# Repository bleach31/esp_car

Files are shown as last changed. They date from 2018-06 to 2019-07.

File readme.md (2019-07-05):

View this project on [CADLAB.io](https://cadlab.io/project/1962). 

### diff drive car by esp-wroom-32

Cuddling Alexa
### software
esp32、androidはソースコードの中

microbit:https://makecode.microbit.org/_AAq7xpe3sfrz

### hardware
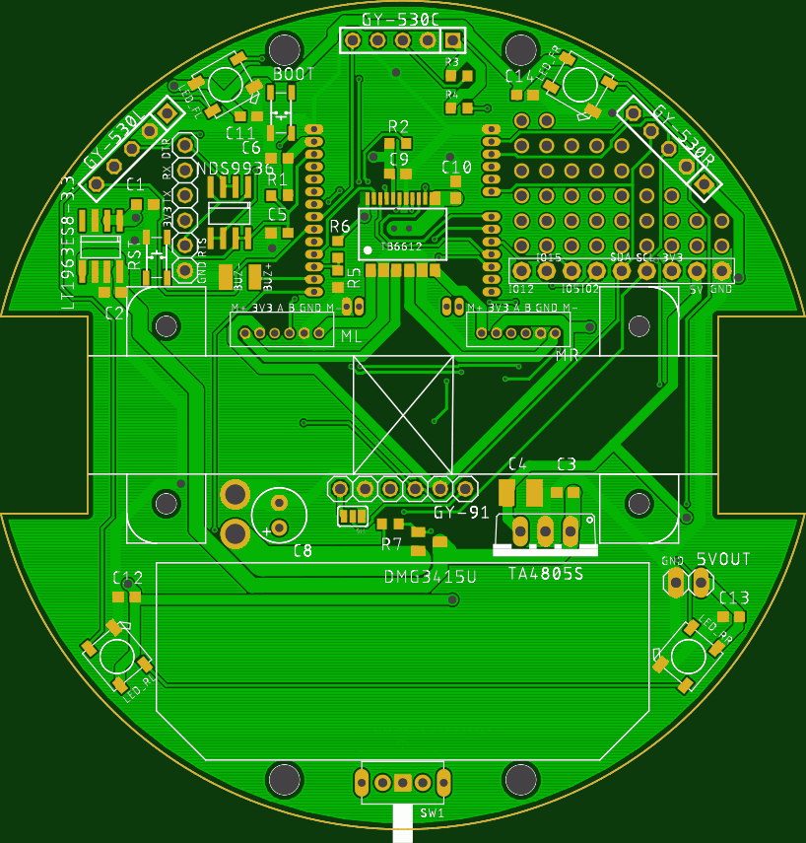
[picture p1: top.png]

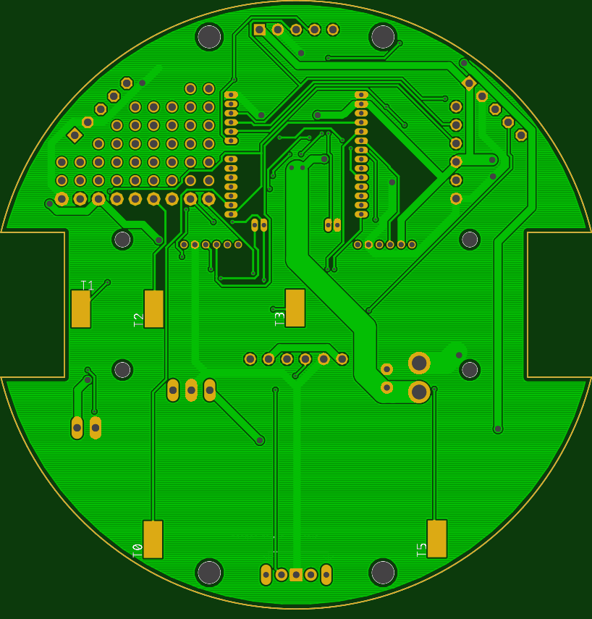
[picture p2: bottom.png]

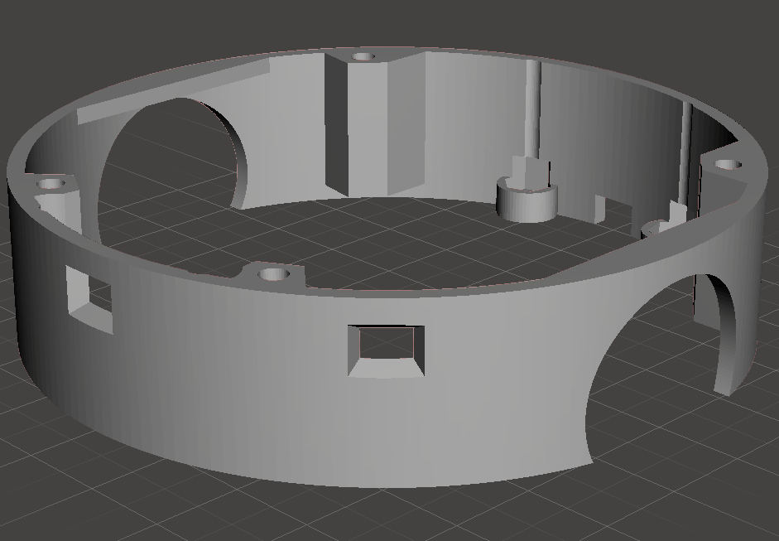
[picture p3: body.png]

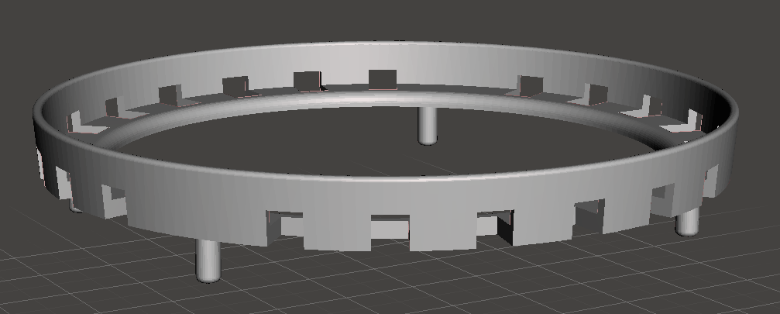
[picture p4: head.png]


モータマウント：https://www.thingiverse.com/thing:1364768
↑の12mmのやつ。

#### parts memo
- 100kオーム 1608 http://akizukidenshi.com/catalog/g/gR-11792/
- 5v 1a 縦型　 http://akizukidenshi.com/catalog/g/gI-00537/
    http://akizukidenshi.com/catalog/g/gM-13536/
    発熱がひどかったのでこっちに変更。6.5vから使えて最大1A、効率90-94%

    3.3V系統もBLEを使うと結構やばい。
    http://akizukidenshi.com/catalog/g/gM-13535/で設計すればよかった。
    
    回路設計時は入手性がよくてリポ2セル(最低6.4v)で動くスイッチングレギュレータ見つけられなかった・・・。

- 電源用mosfet http://akizukidenshi.com/catalog/g/gI-03942/
- 47uF http://akizukidenshi.com/catalog/g/gP-04657/
- 100uF http://akizukidenshi.com/catalog/g/gP-08290/
- モータードライバ　http://akizukidenshi.com/catalog/g/gI-11317/
- 3.3V 1.5A http://akizukidenshi.com/catalog/g/gI-02558/
- mos http://akizukidenshi.com/catalog/g/gI-01233/
- タクトスイッチ：http://akizukidenshi.com/catalog/g/gP-06185/
- モータコネクタzh 6pin　ｘ2：https://www.sengoku.co.jp/mod/sgk_cart/detail.php?code=4A44-P4HR
- リポ　2セル　3.7*2=7.4(6.4v-8.4v)　46ｘ20x 18未満
- LEDフルカラー4つ http://akizukidenshi.com/catalog/g/gI-07915/
- 電源コネクタ 　jstコネクタのメス
- ５Vアウトコネクタ　jstコネクタのメス　https://www.amazon.co.jp/SODIAL-R-10ペアの150mm-JSTコネクタープラグケーブルライン-オス＋メス-RC-BECリポ電池の為/dp/B00O2MPSU4/ref=sr_1_9?ie=UTF8&qid=1531495570&sr=8-9&keywords=jst
- 電源スイッチ, 横向き　http://akizukidenshi.com/catalog/g/gP-08789/
- ブザー http://akizukidenshi.com/catalog/g/gP-04497/
- アレクサ給電用microUSB:　http://www.epanorama.net/newepa/2016/04/27/qi-receiver-teardown/
- モータマウント m2 5mmぐらい4個　, M3　ネジ＋ナット　5㎜ぐらい ４個
- 距離センサ GY-530 3つ　4pin。10.5x13.3 https://www.smart-prototyping.com/VL53L0X-Time-of-Flight-Distance-Sensor-GY-530
- 9軸+気温+気圧　GY-91 (MPU9250+BMP280) 6pin　14.3mm * 20.5mm　https://electronics.semaf.at/9DOF-Axis-IMU-MPU9250-and-BMP280-Atmospheric-Sensor

1608の抵抗10k,20kとか
1608のコンデンサ0.1uF 10uFとか。

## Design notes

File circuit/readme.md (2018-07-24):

修正点メモ

バッテリー電圧検知をADC1にさす。ADC2はWifiBLEと同時使用できない。

ネジ穴をもう少し内側へ

モータコネクタとマイコンの干渉

リセットボタン押しにくい

UARTコネクタとケースの干渉

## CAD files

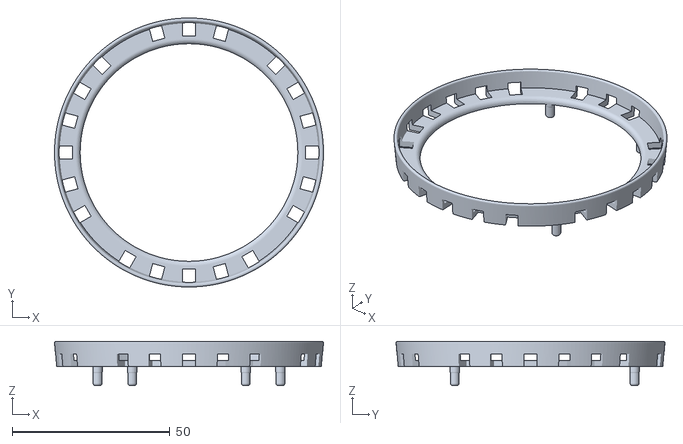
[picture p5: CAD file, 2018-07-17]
hardware/head.stl
85.3 x 85.3 x 14.0

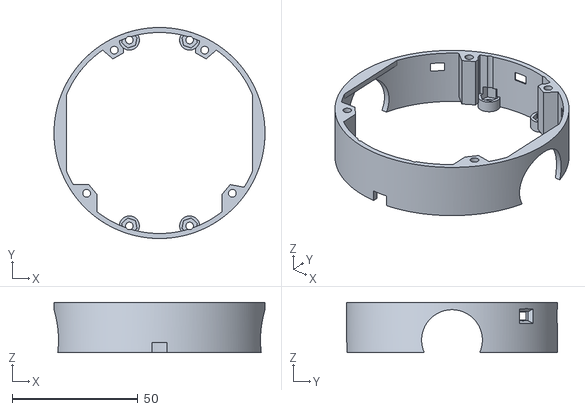
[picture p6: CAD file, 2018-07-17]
hardware/Body.stl
84.0 x 84.0 x 20.0

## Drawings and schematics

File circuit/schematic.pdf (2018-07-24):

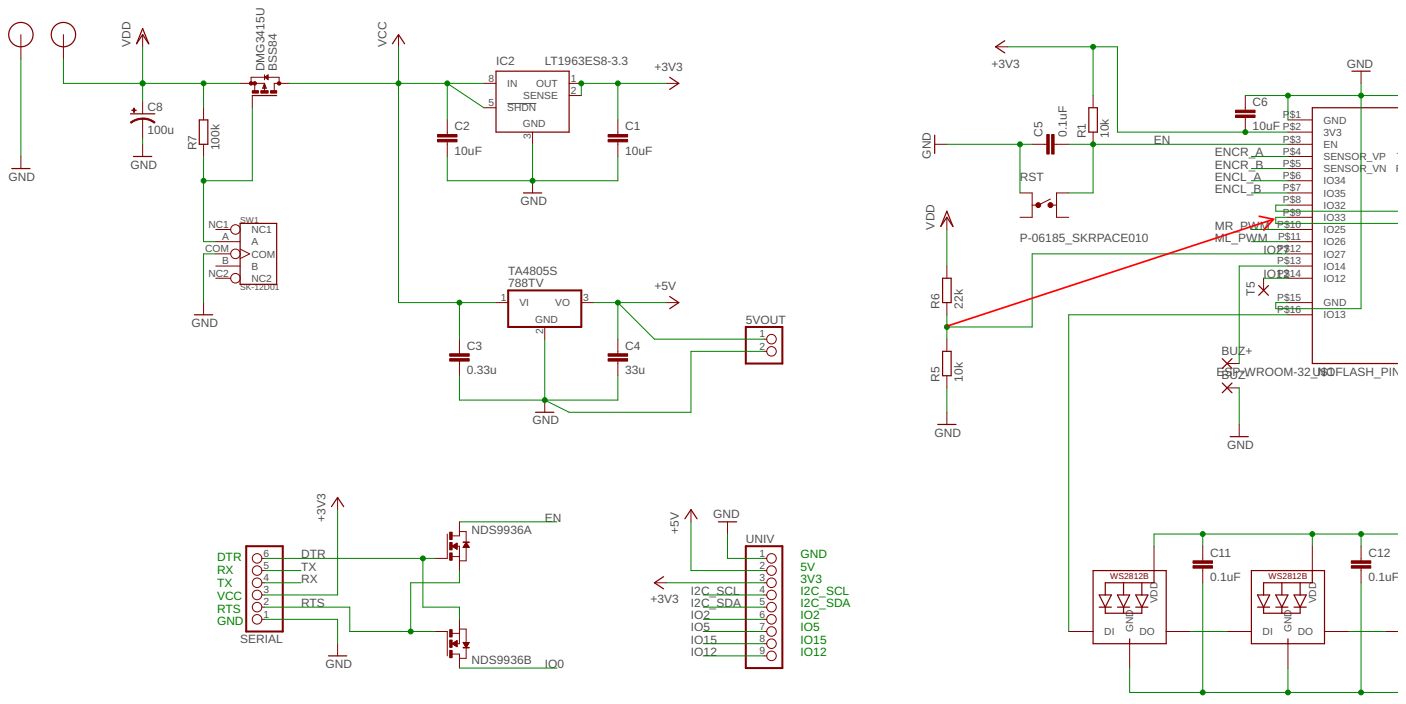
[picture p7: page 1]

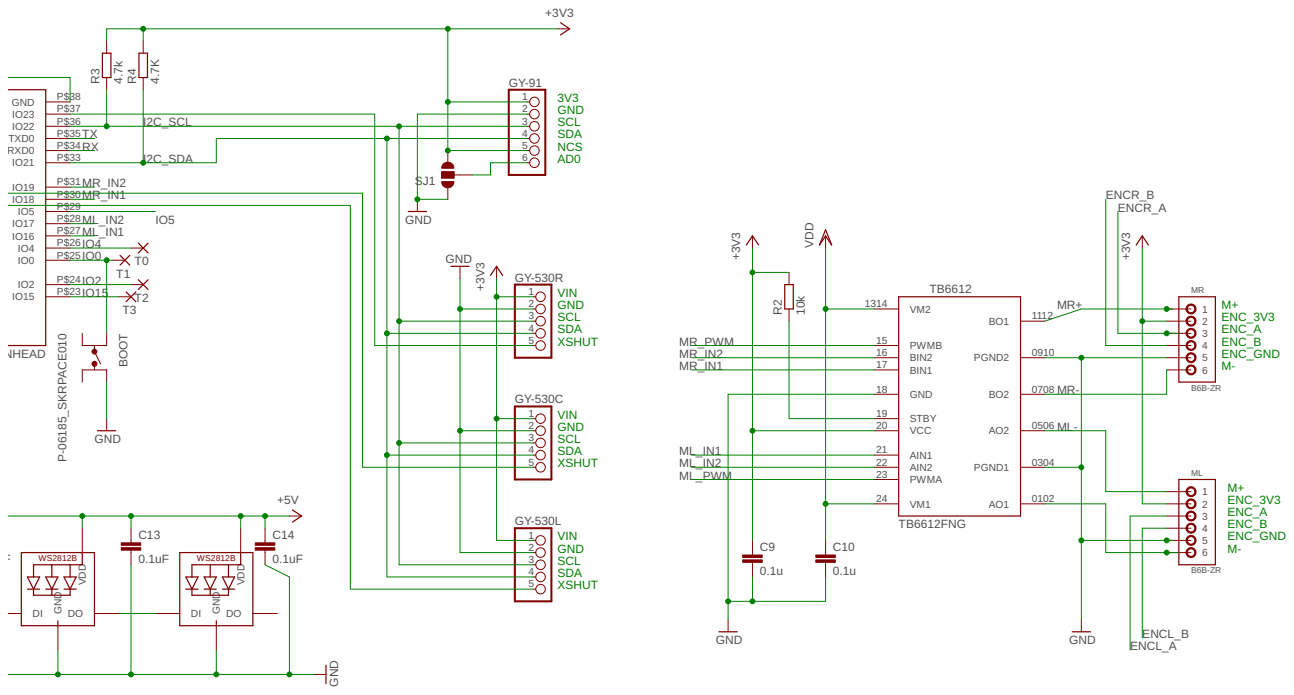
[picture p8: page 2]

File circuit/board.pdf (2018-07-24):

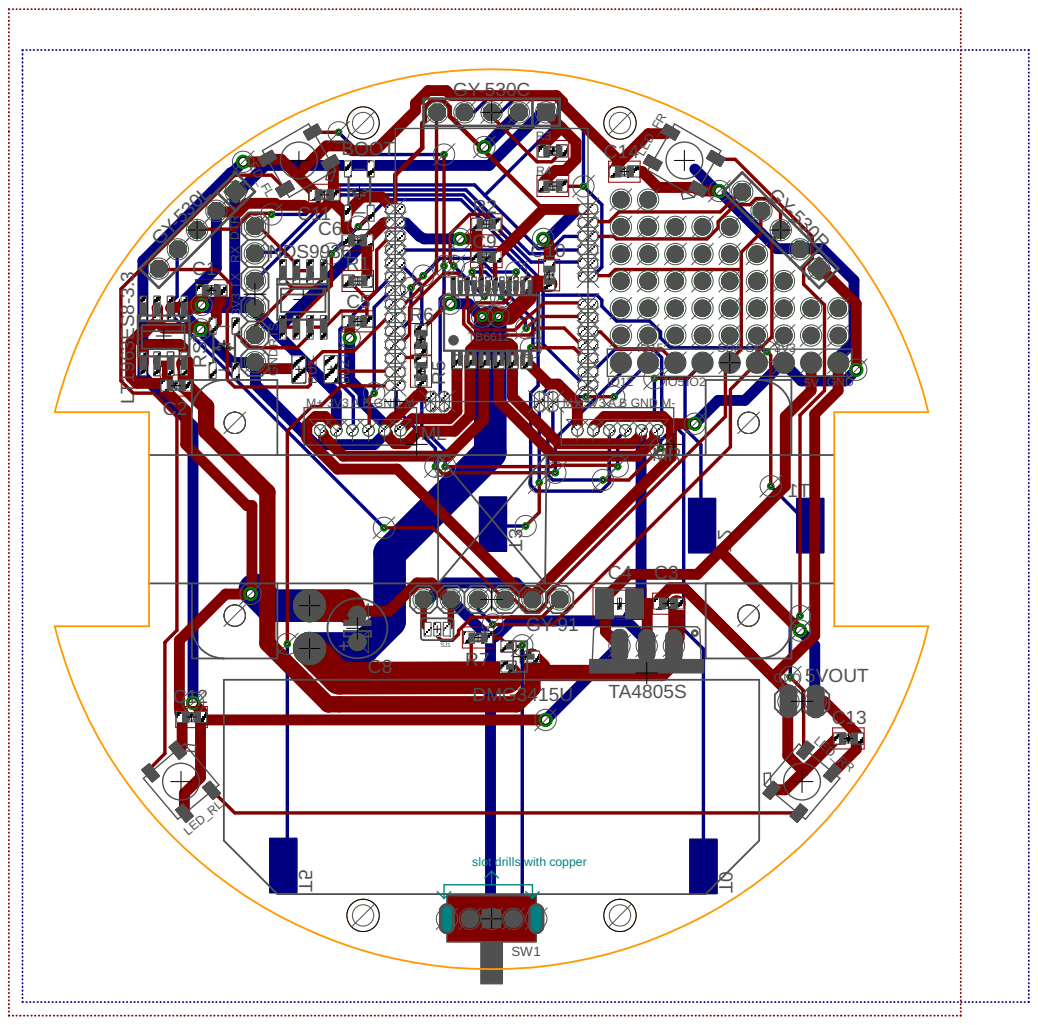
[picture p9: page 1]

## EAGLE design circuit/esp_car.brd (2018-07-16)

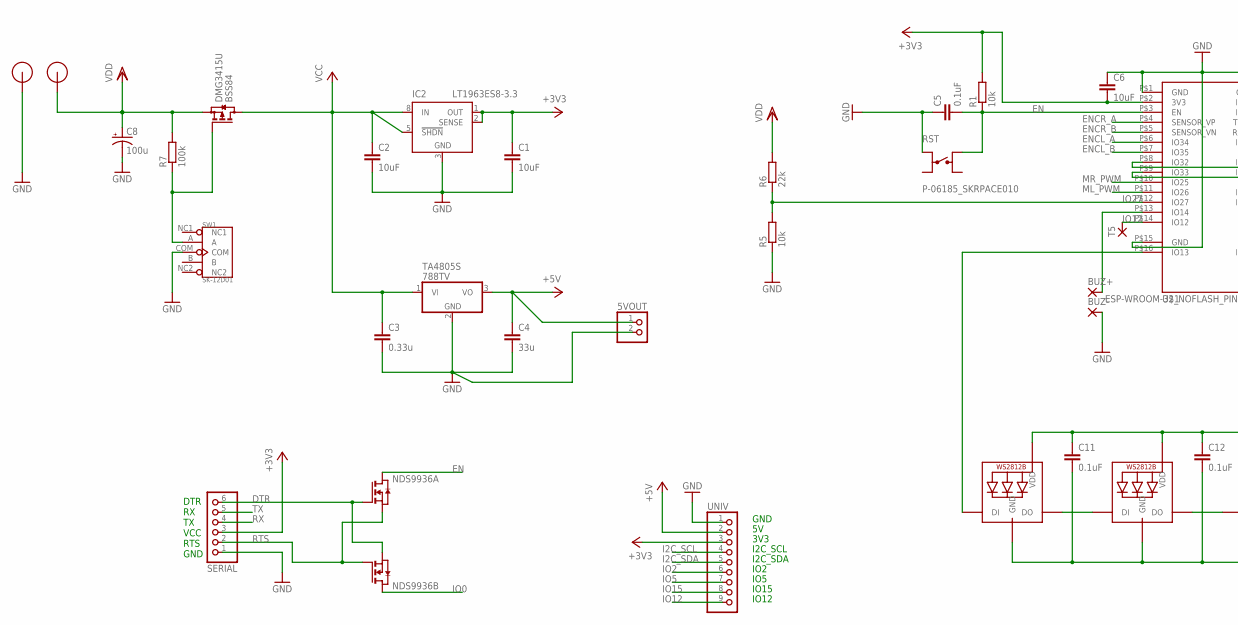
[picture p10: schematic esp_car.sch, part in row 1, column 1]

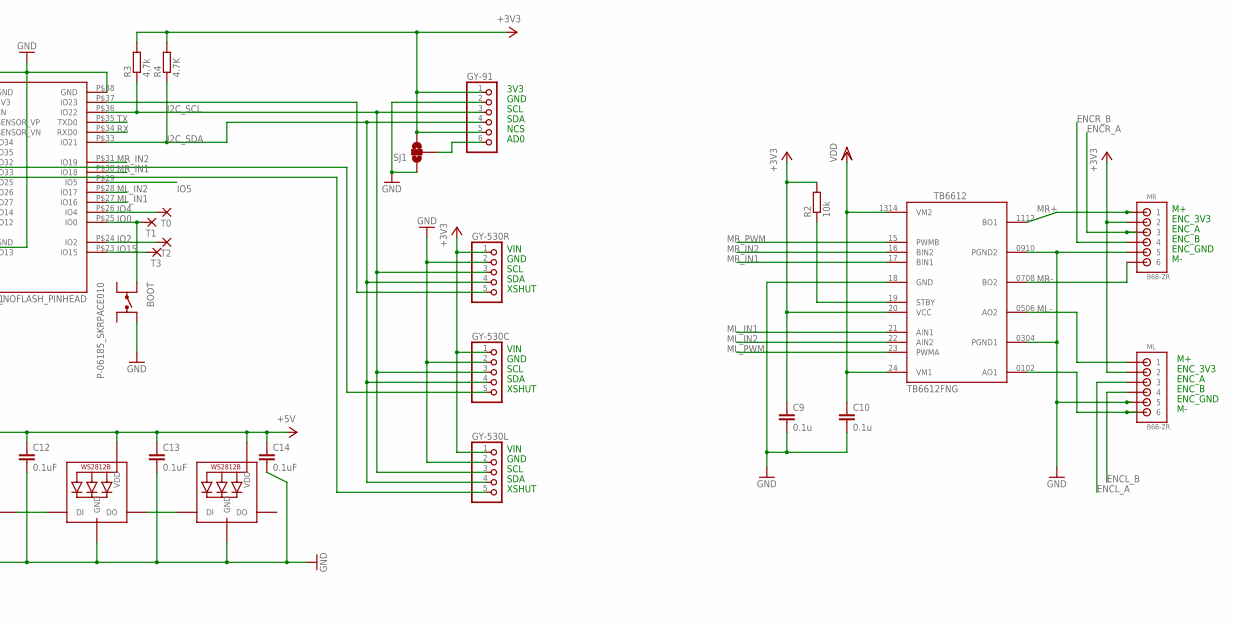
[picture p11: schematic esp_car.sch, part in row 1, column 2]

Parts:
5VOUT: PINHD-1X2; 1X02
BOOT: P-06185_SKRPACE010; SKRP
BUZ+: SMD2; SMD1,27-2,54
BUZ-: SMD2; SMD1,27-2,54
C1, C2, C6: 10uF; C1608
C3: 0.33u; C1608
C4: 33u; C3225
C5, C11, C12, C13, C14: 0.1uF; C1608
C8: 100u; E2,5-6
C9, C10: 0.1u; C1608
DMG3415U: BSS84; SOT23
GY-91: PINHD-1X6; 1X06
GY-530C, GY-530L, GY-530R: PINHD-1X5; 1X05
IC2: LT1963ES8-3.3; SOIC8
LED_FL: WS2812B5050; WS2812B
LED_FR: WS2812B5050; WS2812B
LED_RL: WS2812B5050; WS2812B
LED_RR: WS2812B5050; WS2812B
ML: B6B-ZR
MR: B6B-ZR
NDS9936: NMOS2SO8; SO8
R1, R2, R5: 10k; R0603
R3: 4.7k; R0603
R4: 4.7K; R0603
R6: 22k; R0603
R7: 100k; R0603
RST: P-06185_SKRPACE010; SKRP
SERIAL: PINHD-1X6; 1X06
SJ1: SOLDERJUMPER_2WAYS; SJ_3
SW1: SK-12D01; SW5-2.0-8.8X4.4X4.7MM-90D
T0, T1, T2, T3, T5: SMD5; SMD2,54-5,08
TA4805S: 788TV; TO220V
TB6612: TB6612_NEW; SSOP24_TB6612
U$1: ESP-WROOM-32_NOFLASH_PINHEAD
U$5, U$7: 2.0
UNIV: PINHD-1X9; 1X09-BIG

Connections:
+3V3: C1.1, C6.2, C9.1, GY-91.1, GY-91.5, GY-530C.1, GY-530L.1, GY-530R.1, IC2.1 (OUT), IC2.2 (SENSE), ML.2, MR.2, R1.2, R2.2, R3.2, R4.2, SERIAL.3, SJ1.3, TB6612.20 (VCC), U$1.P$2 (3V3), UNIV.3
+5V: 5VOUT.1, C4.1, C11.1, C12.1, C13.1, C14.1, LED_FL.1-VDD (VDD), LED_FR.1-VDD (VDD), LED_RL.1-VDD (VDD), LED_RR.1-VDD (VDD), TA4805S.3 (VO), UNIV.2
DTR: NDS9936.2 (G), NDS9936.3 (S), SERIAL.6
EN: C5.2, NDS9936.7 (D), NDS9936.8 (D), R1.1, RST.2A, U$1.P$3 (EN)
ENCL_A: ML.3, U$1.P$6 (IO34)
ENCL_B: ML.4, U$1.P$7 (IO35)
ENCR_A: MR.3, U$1.P$4 (SENSOR_VP)
ENCR_B: MR.4, U$1.P$5 (SENSOR_VN)
GND: 5VOUT.2, BOOT.2A, BUZ-.1, C1.2, C2.2, C3.2, C4.2, C5.1, C6.1, C8.-, C9.2, C10.2, C11.2, C12.2, C13.2, C14.2, GY-91.2, GY-530C.2, GY-530L.2, GY-530R.2, IC2.3 (GND), IC2.6 (GND), IC2.7 (GND), LED_FL.3-GND (GND), LED_FR.3-GND (GND), LED_RL.3-GND (GND), LED_RR.3-GND (GND), ML.5, MR.5, R5.1, RST.1A, SERIAL.1, SJ1.1, SW1.COM, TA4805S.2 (GND), TB6612.18 (GND), TB6612.0304 (PGND1), TB6612.0910 (PGND2), U$1.P$1 (GND), U$1.P$15 (GND), U$1.P$38 (GND), U$5.P$1, UNIV.1
I2C_SCL: GY-91.3, GY-530C.3, GY-530L.3, GY-530R.3, R3.1, U$1.P$36 (IO22), UNIV.4
I2C_SDA: GY-91.4, GY-530C.4, GY-530L.4, GY-530R.4, R4.1, U$1.P$33 (IO21), UNIV.5
IO0: BOOT.1A, NDS9936.5 (D), NDS9936.6 (D), T1.1, U$1.P$25 (IO0)
IO2: T2.1, U$1.P$24 (IO2), UNIV.6
IO4: T0.1, U$1.P$26 (IO4)
IO5: U$1.P$29 (IO5), UNIV.7
IO12: T5.1, U$1.P$14 (IO12), UNIV.9
IO15: T3.1, U$1.P$23 (IO15), UNIV.8
IO27: R5.2, R6.1, U$1.P$12 (IO27)
ML-: ML.6, TB6612.0102 (AO1)
ML_IN1: TB6612.21 (AIN1), U$1.P$27 (IO16)
ML_IN2: TB6612.22 (AIN2), U$1.P$28 (IO17)
ML_PWM: TB6612.23 (PWMA), U$1.P$11 (IO26)
MR+: MR.1, TB6612.1112 (BO1)
MR-: MR.6, TB6612.0708 (BO2)
MR_IN1: TB6612.17 (BIN1), U$1.P$30 (IO18)
MR_IN2: TB6612.16 (BIN2), U$1.P$31 (IO19)
MR_PWM: TB6612.15 (PWMB), U$1.P$10 (IO25)
unnamed: GY-530C.5, U$1.P$8 (IO32)
unnamed: GY-91.6, SJ1.2
unnamed: GY-530R.5, U$1.P$37 (IO23)
unnamed: LED_FL.2-DOUT (DO), LED_RL.4-DIN (DI)
unnamed: R2.1, TB6612.19 (STBY)
unnamed: BUZ+.1, U$1.P$13 (IO14)
unnamed: LED_RL.2-DOUT (DO), LED_RR.4-DIN (DI)
unnamed: LED_FR.4-DIN (DI), LED_RR.2-DOUT (DO)
unnamed: LED_FL.4-DIN (DI), U$1.P$16 (IO13)
unnamed: GY-530L.5, U$1.P$9 (IO33)
unnamed: ML.1, TB6612.0506 (AO2)
unnamed: DMG3415U.1 (G), R7.1, SW1.A
RTS: NDS9936.1 (S), NDS9936.4 (G), SERIAL.2
RX: SERIAL.4, U$1.P$34 (RXD0)
TX: SERIAL.5, U$1.P$35 (TXD0)
VCC: C2.1, C3.1, DMG3415U.3 (D), IC2.5 (!SHDN), IC2.8 (IN), TA4805S.1 (VI)
VDD: C8.+, C10.1, DMG3415U.2 (S), R6.2, R7.2, TB6612.24 (VM1), TB6612.1314 (VM2), U$7.P$1

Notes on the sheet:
DTR RX TX VCC RTS GND
ENC_3V3
ENC_A
ENC_B
ENC_GND
3V3
GND
SCL
SDA
NCS
AD0
VIN
XSHUT
I2C_SCL
I2C_SDA
IO2
IO5
IO15
IO12

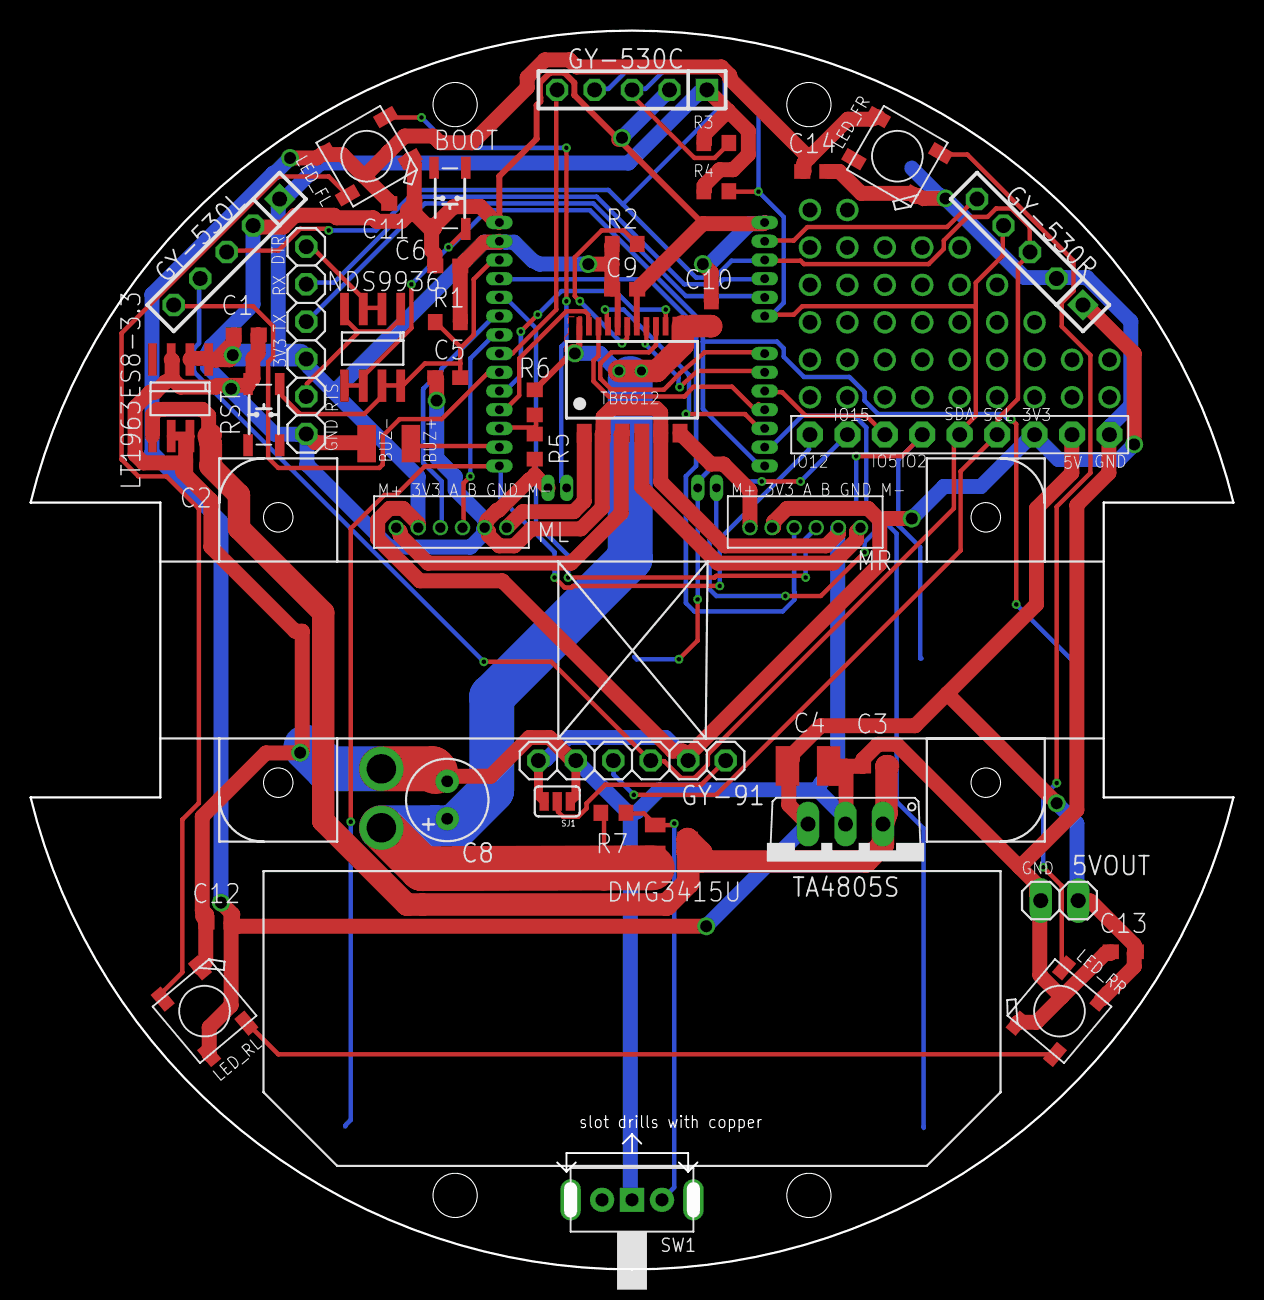
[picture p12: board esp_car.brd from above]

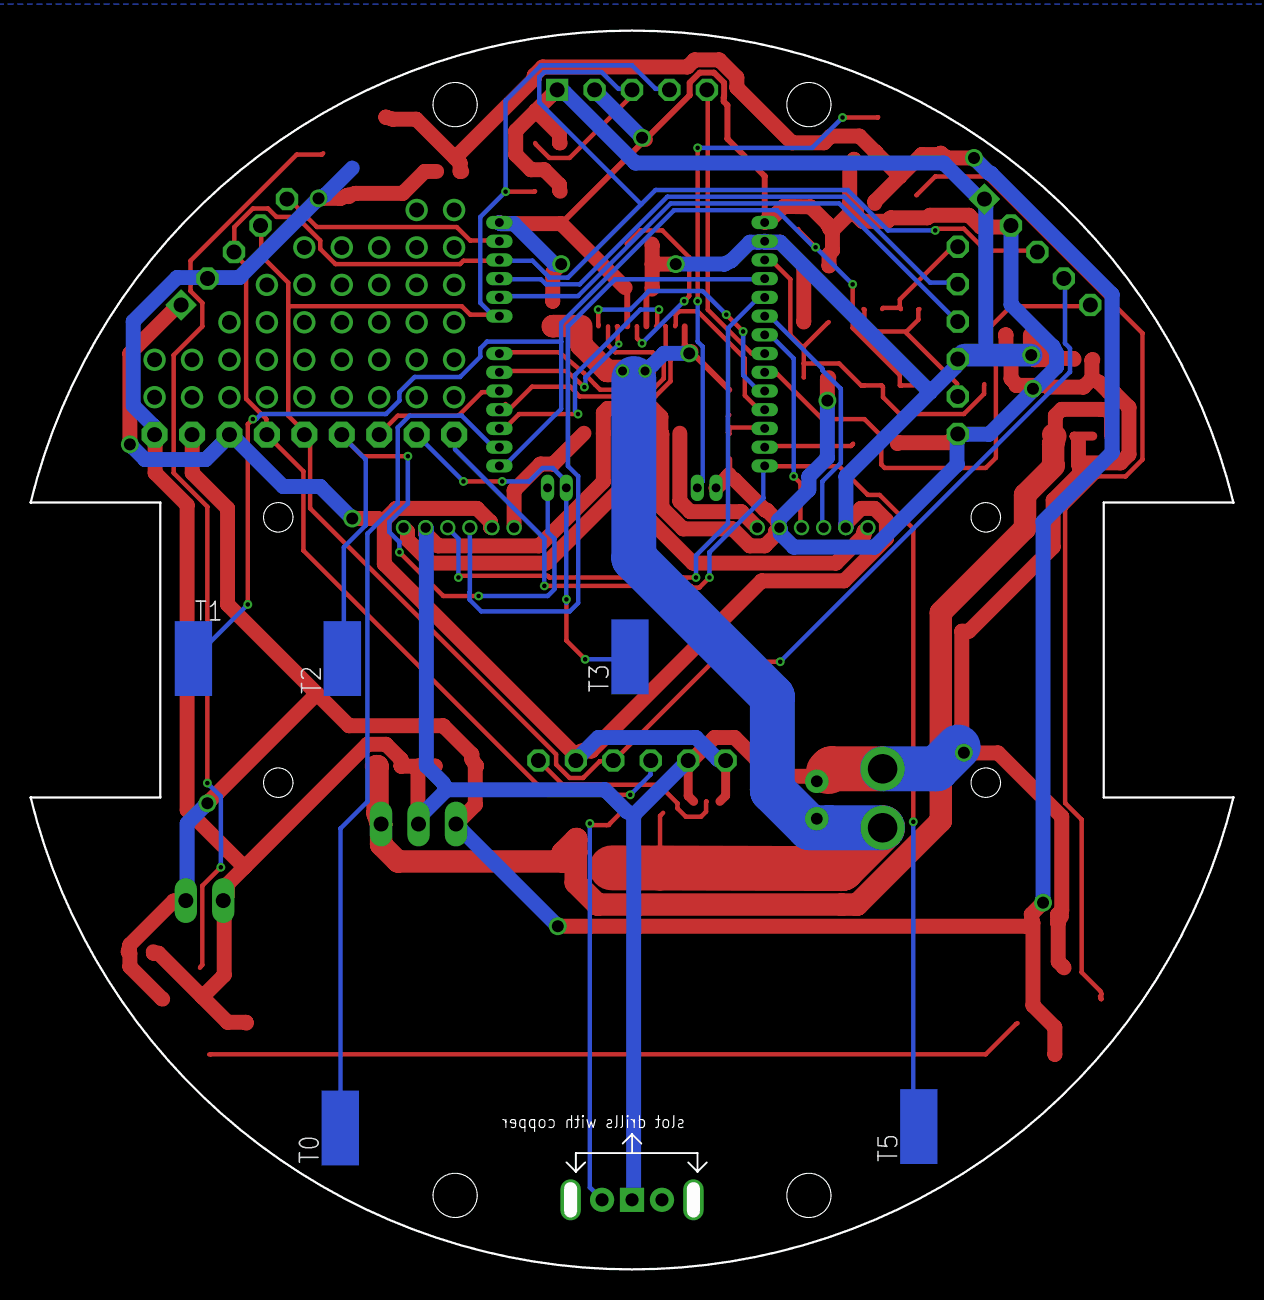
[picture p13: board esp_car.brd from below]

Board: 2 copper layers, 81.6 x 84.0 mm, 52 parts (5 on the bottom side), 44 nets.

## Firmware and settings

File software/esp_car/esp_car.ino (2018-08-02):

//#define ESP32
#include "esp_deep_sleep.h"
//#define DEBUG
//////////////////////////Motor//////////////////////
#include "SparkFun_TB6612.h"
Motor MotorR = Motor(GPIO_NUM_18, GPIO_NUM_19, GPIO_NUM_25, 0, 1); //制御ピン18，19, PWMピン25
Motor MotorL = Motor(GPIO_NUM_16, GPIO_NUM_17, GPIO_NUM_26, 1, 1); //制御ピン16，17, PWMピン26
//制御用目標RPM　-90～90ぐらい
double rpm_trg_L = 0;
double rpm_trg_R = 0;
/////////////////////////LED///////////////////////
#include "Adafruit_NeoPixel.h"
#define LEDNUM 4
Adafruit_NeoPixel pixels = Adafruit_NeoPixel(LEDNUM, GPIO_NUM_13, NEO_GRB + NEO_KHZ800);

uint32_t red = pixels.Color(255, 0, 0);
uint32_t orange = pixels.Color(255, 165, 0);
uint32_t yellow = pixels.Color(255, 255, 0);
uint32_t green = pixels.Color(0, 128, 0);
uint32_t cyan = pixels.Color(0, 255, 255);
uint32_t blue = pixels.Color(0, 0, 255);
uint32_t purple = pixels.Color(128, 0, 128);

/////////////////////////I2C///////////////////////
#include <Wire.h>
TwoWire I2C = TwoWire(0);
/////////////////////////IMU///////////////////////
#include "MPU9250_asukiaaa.h"
MPU9250 mpu;
float aX, aY, aZ, aSqrt, gX, gY, gZ, mDirection, mX, mY, mZ;
/////////////////////////ToF//////////////////////
#include "VL53L0X.h"
VL53L0X tof_c;

//int tof_c_xshut = 32;//GPIO32 とりあえず1個運用

////////////////////////battery////////////////
int BAT_PIN = GPIO_NUM_33;
double vbat;

///////////////////////ENC/////////////////////
#include "qei.hpp"
double rpm_L = 0;
double rpm_R = 0;
hw_timer_t *timer = NULL;
TaskHandle_t th[2];

///////////////////////Touch/////////////////
uint8_t touchThr = 20;

/////////////////////////BLE///////////////////////
#include <BLEDevice.h>
#include <BLEServer.h>
#include <BLEUtils.h>
#include <BLE2902.h>

#include <string.h>

BLEServer *pServer = NULL;
BLECharacteristic *pTxCharacteristic;
bool deviceConnected = false;
bool oldDeviceConnected = false;
uint8_t txValue = 0;

#define SERVICE_UUID "8ff3d648-3ce2-4013-874a-4162cd85300d" // UART service UUID
#define CHARACTERISTIC_UUID_RX "f35a5414-d140-447b-90e9-3e0263ac7a05"
#define CHARACTERISTIC_UUID_TX "dd673cd0-24bf-4421-95d5-67bb3ab1f3d6"

// USE Centralモード

//static BLEUUID ubit_serviceUUID("E95D0753-251D-470A-A062-FA1922DFA9A8");
//static BLEUUID     ubit_accUUID("E95Dca4b-251D-470A-A062-FA1922DFA9A8");
static BLEUUID ubit_serviceUUID("6e400001-b5a3-f393-e0a9-e50e24dcca9e");
static BLEUUID ubit_uartUUID("6e400002-b5a3-f393-e0a9-e50e24dcca9e");
static BLEAddress *pServerAddress = new BLEAddress("e0:73:d3:8f:72:29");
static BLERemoteCharacteristic *pRemoteCharacteristic;

class MyServerCallbacks : public BLEServerCallbacks
{
	void onConnect(BLEServer *pServer)
	{
		deviceConnected = true;
	};

	void onDisconnect(BLEServer *pServer)
	{
		deviceConnected = false;
	}
};
class MyCallbacks : public BLECharacteristicCallbacks
{
	void onWrite(BLECharacteristic *pCharacteristic)
	{
		//String rxValue = pCharacteristic->getValue();
		std::string rxValue = pCharacteristic->getValue();

		if (rxValue.length() > 0)
		{

			int sep = rxValue.find(",");
			const char *xChar = rxValue.substr(0, sep).c_str();
			const char *yChar = rxValue.substr(sep + 1).c_str();

			float x = strtof(xChar, NULL) / 9.8; //ms^2 to G
			float y = strtof(yChar, NULL) / 9.8; //ms^2 to G

			//不感帯
			if (-0.1 < x && x < 0.1)
				x = 0;
			if (-0.1 < y && y < 0.1)
				y = 0;

			rpm_trg_L = y * -50 + x * -50;
			rpm_trg_R = y * -50 + x * 50;

			/*
			Serial.print(" x:");
			Serial.print(x);
			Serial.print(" y:");
			Serial.print(y);
			Serial.println("");
			*/
		}
	}
};

static void notifyCallback(
	BLERemoteCharacteristic *pBLERemoteCharacteristic,
	uint8_t *pData,
	size_t length,
	bool isNotify)
{
	/*
	Serial.print("Notify callback for characteristic: ");
	//Serial.print(pBLERemoteCharacteristic->getUUID().toString().c_str());
	Serial.print(" of data length ");
	Serial.print(length);
	Serial.print(" data: ");

	for(int i = 0;i < length ;i++)
	{
		Serial.print((char)pData[i]);
	}
	*/
	//pdataに前回の値が残ってる事があるのでいったん配列にコピー
	char pChar[length + 1];
	memcpy(pChar, pData, length);
	pChar[length] = '\0';

	std::string str = pChar;

	/*
	Serial.print(" String Value: ");
	for (int i = 0; i < str.length(); i++)
		Serial.print(str[i]);
	*/

	int sep = str.find(",");

	const char *xChar = str.substr(0, sep).c_str();
	const char *yChar = str.substr(sep + 1).c_str();

	float x = strtof(xChar, NULL) / 1000; //mG to G
	float y = strtof(yChar, NULL) / 1000; //mG to G

	/*
	Serial.print(" x:");
	Serial.print(x);
	Serial.print(" y:");
	Serial.print(y);
	Serial.print("");
	*/
	//不感帯
	if (-0.1 < x && x < 0.1)
		x = 0;
	if (-0.1 < y && y < 0.1)
		y = 0;

	rpm_trg_L = y * -50 + x * 50;
	rpm_trg_R = y * -50 + x * -50;

	/*
	Serial.println("");
	int16_t sx, sy, sz;//-1000 ~ 1000

	memcpy(&sx, &pData[0], 2);
	memcpy(&sy, &pData[2], 2);
	memcpy(&sz, &pData[4], 2);
	Serial.print("\t");
	Serial.print(sx);
	Serial.print("\t");
	Serial.print(sy);
	Serial.print("\t");
	Serial.print(sz);


	float x = (float)sx / 100.0; //-10 ~ 10
	float y = (float)sy / 100.0; //-10 ~ 10


	//不感帯
	if (-1 < x && x < 1)
		x = 0;
	if (-1 < y && y < 1)
		y = 0;

	rpm_trg_L = y * -5 + x * -5;
	rpm_trg_R = y * -5 + x * 5;


	Serial.print("\t");
	Serial.print(rpm_trg_L);
	Serial.print("\t");
	Serial.print(rpm_trg_R);
	*/
}

///////////////////////Mode///////////////////
enum Mode
{
	DEMO,
	FOLLOW,
	RC,
	INIT,
	RC_Central
};
enum Mode mode = INIT;
enum Mode pre_mode = INIT;

void gotTouch0()
{
	mode = DEMO;
}
void gotTouch2()
{
	mode = RC_Central;
}

void gotTouch3()
{
	mode = RC;
}

void gotTouch5()
{
	mode = FOLLOW;
}

//遅い周期タスク,RPM測定、バッテリー測定
void loop_slow(void *pvParameters)
{
	TickType_t xLastWakeTime;
	const TickType_t xFrequency = 100 / portTICK_PERIOD_MS;
	// Initialise the xLastWakeTime variable with the current time.
	xLastWakeTime = xTaskGetTickCount();

	while (true)
	{

		//RPM
		uint64_t time_now;
		int16_t count_L;
		int16_t count_R;

		time_now = timerRead(timer);
		pcnt_get_counter_value(PCNT_UNIT_0, &count_L);
		pcnt_get_counter_value(PCNT_UNIT_1, &count_R);

		rpm_L = (double)(count_L) / ((double)time_now / 10000.0);
		rpm_R = (double)(count_R) / ((double)time_now / 10000.0);

		//タイマーとカウンターのリセット
		timer = timerBegin(0, 80, true); //80分周で1usec
		pcnt_counter_clear(PCNT_UNIT_0);
		pcnt_counter_clear(PCNT_UNIT_1);

		/*
		Serial.print("RPM L:");
		Serial.print(rpm_L);
		Serial.print(" R:");
		Serial.print(rpm_R);
		*/

		//バッテリー値
		vbat = ((double)analogRead(BAT_PIN) / 4095) * ((35.0) / 10.0) * 3.3; //35/10はは抵抗値の適合後の値
		if (vbat < 6.4)
		{
			rpm_trg_L = 0;
			rpm_trg_R = 0;
			pixels.clear();
			delay(100);

			//Serial.print(" low battery\n");

			// スリープのための諸々の設定(今回はGPIO0ピンを使う)
			esp_deep_sleep_pd_config(ESP_PD_DOMAIN_RTC_PERIPH, ESP_PD_OPTION_OFF);
			esp_deep_sleep_pd_config(ESP_PD_DOMAIN_RTC_SLOW_MEM, ESP_PD_OPTION_OFF);
			esp_deep_sleep_pd_config(ESP_PD_DOMAIN_RTC_FAST_MEM, ESP_PD_OPTION_OFF);
			esp_deep_sleep_pd_config(ESP_PD_DOMAIN_MAX, ESP_PD_OPTION_OFF);

			esp_deep_sleep_start(); // スリープモード実行（Wakeupオプションなし＝外部リセットまで）
		}
		// Wait for the next cycle.
		vTaskDelayUntil(&xLastWakeTime, xFrequency);
	}
}

//速い周期タスク（速度制御）
void loop_fast(void *pvParameters)
{
	TickType_t xLastWakeTime;
	const TickType_t xFrequency = 20 / portTICK_PERIOD_MS;
	// Initialise the xLastWakeTime variable with the current time.
	xLastWakeTime = xTaskGetTickCount();

	while (true)
	{

		//制御　FF　+　P制御
		if (-1 < rpm_trg_L && rpm_trg_L < 1)
		{
			MotorL.brake();
		}
		else
		{
			//FF　90rpmで8vぐらい。FB誤差補正
			double trg_v = rpm_trg_L * 0.09 + (rpm_trg_L - rpm_L) * 0.02;
			MotorL.drive(((int)((trg_v * 1000) / vbat)));
			/*
			Serial.print("\t\t\t\t\t\t\t\t\t\t\t\t");
			Serial.print(trg_v);
			Serial.print("\t");
			Serial.print(((int)((trg_v*1000) / vbat)));
			Serial.println("");
			*/
		}

		if (-1 < rpm_trg_R && rpm_trg_R < 1)
		{
			MotorR.brake();
		}
		else
		{
			double trg_v = rpm_trg_R * 0.09 + (rpm_trg_R - rpm_R) * 0.02;
			MotorR.drive(((int)((trg_v * 1000) / vbat)));
		}

		// Wait for the next cycle.
		vTaskDelayUntil(&xLastWakeTime, xFrequency);
	}
}

void debug()
{

	Serial.print("TrgRPM L:");
	Serial.print(rpm_trg_L);
	Serial.print(" R:");
	Serial.print(rpm_trg_R);

	Serial.print(" T0:");
	Serial.print(touchRead(T0));
	Serial.print(" T1:");
	Serial.print(touchRead(T1));
	Serial.print(" T2:");
	Serial.print(touchRead(T2));
	Serial.print(" T3:");
	Serial.print(touchRead(T3));
	Serial.print(" T5:");
	Serial.print(touchRead(T5));

	int16_t count_L;
	int16_t count_R;
	pcnt_get_counter_value(PCNT_UNIT_2, &count_L);
	pcnt_get_counter_value(PCNT_UNIT_3, &count_R);

	Serial.print(" Pulse L:");
	Serial.print(count_L);
	Serial.print(" R:");
	Serial.print(count_R);
	Serial.print(" ");
	/*
	mpu.accelUpdate();
	aX = mpu.accelX();
	aY = mpu.accelY();
	aZ = mpu.accelZ();
	aSqrt = mpu.accelSqrt();
	Serial.print(" accelX: " + String(aX) + " accelY: " + String(aY) + " accelZ: " + String(aZ));
	Serial.print(" accelSqrt: " + String(aSqrt));
	Serial.print(" ");

	mpu.gyroUpdate();
	gX = mpu.gyroX();
	gY = mpu.gyroY();
	gZ = mpu.gyroZ();
	Serial.print(" gyroX: " + String(gX) + " gyroY: " + String(gY) + " gyroZ: " + String(gZ));
	Serial.print(" ");

	mpu.magUpdate();
	mX = mpu.magX();
	mY = mpu.magY();
	mZ = mpu.magZ();
	mDirection = mpu.magHorizDirection();
	Serial.print(" magX: " + String(mX) + " maxY: " + String(mY) +" magZ: " + String(mZ));
	Serial.print("horizontal direction: " + String(mDirection));
	*/

	uint16_t dist_c = tof_c.readRangeSingleMillimeters();
	Serial.print(" dist:");
	Serial.print(dist_c);

	Serial.print(" vbat:");
	Serial.print(vbat);

	Serial.println("");
}

uint8_t lost_flag = 2 ^ 4;
void following()
{
	//////////////////////距離取得
	uint16_t dist_c = tof_c.readRangeSingleMillimeters();
	//if (tof_c.timeoutOccurred()) { Serial.print(" TIMEOUT"); }

#ifdef DEBUG
	Serial.print(" dist:");
	Serial.println(dist_c);
#endif

	if (dist_c > 8000) // lost -> search object
	{
		lost_flag /= 2; //5以上割ったら0

		while (mode == FOLLOW && lost_flag <= 0) //5連続でロスト判定
		{
			//走査しながら左旋回
			pcnt_counter_clear(PCNT_UNIT_2);
			pcnt_counter_clear(PCNT_UNIT_3);
			for (int e = 0; e < LEDNUM; e++)
			{
				pixels.setPixelColor(e, purple);
				pixels.show();
			}

			rpm_trg_L = -20;
			rpm_trg_R = 20;

			uint16_t dist_min = 65535;
			int16_t count_L_rem = 0;
			int16_t count_R_rem = 0;
			int16_t count_R = 0;

			while (mode == FOLLOW)
			{
#ifdef DEBUG
				Serial.print("L:");
				Serial.print(count_L_rem);
				Serial.print("R:");
				Serial.println(count_R_rem);
#endif

				uint16_t dist_c = tof_c.readRangeSingleMillimeters();
				//最大距離とその時のエンコーダの値を記憶
				if (dist_c < dist_min)
				{
					dist_min = dist_c;
					pcnt_get_counter_value(PCNT_UNIT_2, &count_L_rem);
					pcnt_get_counter_value(PCNT_UNIT_3, &count_R_rem);
				}
				pcnt_get_counter_value(PCNT_UNIT_3, &count_R);
				if (count_R > 1500) //:TODO 約1回転ほど進んだら抜ける
				{
					break;
				}
				delay(1);
			}

			for (int e = 0; e < LEDNUM; e++)
			{
				pixels.setPixelColor(e, cyan);
				pixels.show();
			}

			//記憶した位置まで右旋回して戻る
			rpm_trg_L = 20;
			rpm_trg_R = -20;
			while (mode == FOLLOW)
			{
				pcnt_get_counter_value(PCNT_UNIT_3, &count_R);
				if (count_R < count_R_rem)
				{
					break;
				}
				delay(1);
			}
			//距離を確認して記憶した最小値＋100mmに物体があれば抜け、だめなら再試行
			uint16_t dist_c = tof_c.readRangeSingleMillimeters();
			if (dist_c < (dist_min + 100))
			{
				break;
			}
		}
	}
	else if (dist_c < 50) //near -> stop
	{
		lost_flag = 2 ^ 4;
		rpm_trg_L = 0;
		rpm_trg_R = 0;
		for (int e = 0; e < LEDNUM; e++)
		{
			pixels.setPixelColor(e, yellow);
			pixels.show();
		}
	}
	else if (dist_c < 2000) //2m まで　follow
	{
		lost_flag = 2 ^ 4;
		//distが最大2000なので目標値が20~60　rpmぐらい。
		rpm_trg_L = dist_c / 50 + 20;
		rpm_trg_R = dist_c / 50 + 20;

		for (int e = 0; e < LEDNUM; e++)
		{
			pixels.setPixelColor(e, red);
			pixels.show();
		}
	}
}

void ble_peripheral_setup()
{
	// Create the BLE Device
	BLEDevice::init("UART Service");

	// Create the BLE Server
	pServer = BLEDevice::createServer();
	pServer->setCallbacks(new MyServerCallbacks());

	// Create the BLE Service
	BLEService *pService = pServer->createService(SERVICE_UUID);

	// Create a BLE Characteristic
	pTxCharacteristic = pService->createCharacteristic(
		CHARACTERISTIC_UUID_TX,
		BLECharacteristic::PROPERTY_NOTIFY);

	pTxCharacteristic->addDescriptor(new BLE2902());

	BLECharacteristic *pRxCharacteristic = pService->createCharacteristic(
		CHARACTERISTIC_UUID_RX,
		BLECharacteristic::PROPERTY_WRITE);

	pRxCharacteristic->setCallbacks(new MyCallbacks());

	// Start the service
	pService->start();
	// Start advertising
	pServer->getAdvertising()->start();
	Serial.println("Waiting a client connection to notify...");
}

void ble_peripheral_loop()
{
	// disconnecting
	if (!deviceConnected && oldDeviceConnected)
	{
		rpm_trg_L = 0;
		rpm_trg_R = 0;
		pixels.clear();
		pixels.setPixelColor(0, blue);
		pixels.show();
		delay(500);					 // give the bluetooth stack the chance to get things ready
		pServer->startAdvertising(); // restart advertising
		Serial.println("restart advertising");
		oldDeviceConnected = deviceConnected;
	}
	// connecting
	if (deviceConnected && !oldDeviceConnected)
	{
		for (int e = 0; e < LEDNUM; e++)
		{
			pixels.setPixelColor(e, blue);
			pixels.show();
		}
		// do stuff here on connecting
		oldDeviceConnected = deviceConnected;
	}
}

void ble_central_setup()
{

	BLEDevice::init("");

	Serial.print("Forming a connection to ");
	Serial.println((*pServerAddress).toString().c_str());

	BLEClient *pClient = BLEDevice::createClient();
	Serial.println(" - Created client");

	// Connect to the  BLE Server.
	pClient->connect(*pServerAddress);
	Serial.println(" - Connected to server");

	// Obtain a reference to the service we are after in the remote BLE server.
	BLERemoteService *pRemoteService = pClient->getService(ubit_serviceUUID);
	if (pRemoteService == nullptr)
	{
		Serial.print("Failed to find our service UUID: ");
		Serial.println(ubit_serviceUUID.toString().c_str());
	}
	Serial.println(" - Found our service");

	// Obtain a reference to the characteristic in the service of the remote BLE server.
	pRemoteCharacteristic = pRemoteService->getCharacteristic(ubit_uartUUID);
	if (pRemoteCharacteristic == nullptr)
	{
		Serial.print("Failed to find our characteristic UUID: ");
		Serial.println(ubit_uartUUID.toString().c_str());
	}
	Serial.println(" - Found our characteristic");

	//enable indicate/notify
	BLERemoteDescriptor *pRD = pRemoteCharacteristic->getDescriptor(BLEUUID((uint16_t)0x2902));
	if (pRD == nullptr)
	{
		Serial.print("Failed to find our descriptor UUID: ");
		Serial.println(BLEUUID((uint16_t)0x2902).toString().c_str());
		for (;;)
			;
	}

	uint8_t data[2] = {0x02, 0x00}; //0x01 0x00 -> notify
	pRD->writeValue(data, 2, false);
	deviceConnected = true;
	for (int e = 0; e < LEDNUM; e++)
	{
		pixels.setPixelColor(e, blue);
		pixels.show();
	}
	// Read the value of the characteristic.
	std::string value = pRemoteCharacteristic->readValue();
	//Serial.print("The characteristic value was: ");
	//Serial.println(value.c_str());

	pRemoteCharacteristic->registerForNotify(notifyCallback);
}

void demo()
{
	//////////////////////距離取得
	uint16_t dist_c = tof_c.readRangeSingleMillimeters();
	//スタック判定

	int16_t count_L = 0;
	pcnt_get_counter_value(PCNT_UNIT_2, &count_L);
#ifdef DEBUG
	Serial.print("Pulse L:");
	Serial.println(count_L);
#endif

	if (abs(count_L) < 20)
	{
		dist_c = 0;
	}

	pcnt_counter_clear(PCNT_UNIT_2);

	if (dist_c > 30)
	{ //まっすぐ進む
		for (int e = 0; e < LEDNUM; e++)
		{
			pixels.setPixelColor(e, orange);
			pixels.show();
		}
		rpm_trg_L = 10;
		rpm_trg_R = 10;
		
		delay(100);
	}
	else
	{
		for (int e = 0; e < LEDNUM; e++)
		{
			pixels.setPixelColor(e, cyan);
			pixels.show();
		}
		//適当な方向に適当な時間だけ回転する
		if (random(0, 100) > 50)
		{
			rpm_trg_L = -10;
			rpm_trg_R = 10;
		}
		else
		{
			rpm_trg_L = 10;
			rpm_trg_R = -10;
		}
		delay(random(500, 3000));
	}
}
//////////////////////////setup/////////////////////

void setup()
{
#ifdef DEBUG
	Serial.begin(115200);
#endif

	//RPM用
	qei_setup_x4(PCNT_UNIT_0, GPIO_NUM_35, GPIO_NUM_34); //LEFT
	qei_setup_x4(PCNT_UNIT_1, GPIO_NUM_39, GPIO_NUM_36); //RIGHT

	//制御用
	qei_setup_x1(PCNT_UNIT_2, GPIO_NUM_35, GPIO_NUM_34);
	qei_setup_x1(PCNT_UNIT_3, GPIO_NUM_39, GPIO_NUM_36);

	//タイマー
	timer = timerBegin(0, 80, true); //80分周で1usec

	//タスク設定 taskNO_AFFINITYでコア選択はスケジューラに委託
	xTaskCreatePinnedToCore(loop_fast, "loop_fast", 2048, NULL, 2, &th[0], tskNO_AFFINITY);
	xTaskCreatePinnedToCore(loop_slow, "loop_slow", 2048, NULL, 3, &th[0], tskNO_AFFINITY);

	//LED
	pixels.begin();			  // This initializes the NeoPixel library.
	pixels.setBrightness(32); //0-255
	pixels.clear();
	pixels.setPixelColor(0, red);

	//IMU
	I2C.begin(GPIO_NUM_21, GPIO_NUM_22, 400000); // SDA, SCL

	mpu.setWire(&I2C);
	mpu.beginAccel();
	mpu.beginGyro();
	mpu.beginMag();

	//ToF
	tof_c.setWire(&I2C);
	tof_c.init();
	tof_c.setTimeout(500);
	// LONG RANGE MODE
	// lower the return signal rate limit (default is 0.25 MCPS)
	tof_c.setSignalRateLimit(0.1);
	// increase laser pulse periods (defaults are 14 and 10 PCLKs)
	tof_c.setVcselPulsePeriod(VL53L0X::VcselPeriodPreRange, 18);
	tof_c.setVcselPulsePeriod(VL53L0X::VcselPeriodFinalRange, 14);

	//Touch
	touchAttachInterrupt(T0, gotTouch0, touchThr);
	touchAttachInterrupt(T2, gotTouch2, touchThr);
	touchAttachInterrupt(T3, gotTouch3, touchThr);
	touchAttachInterrupt(T5, gotTouch5, touchThr);
}

void loop()
{

	//モードごとの定期処理
	switch (mode)
	{
	case INIT:
	{
		debug();
		break;
	}
	case DEMO:
	{
		demo();
		break;
	}
	case FOLLOW:
	{ //呼び出し関数内部でループする場合,while(mode == {xxx})とし、モード変更時に抜けられるようにする
		following();
		break;
	}
	case RC:
	{
		ble_peripheral_loop();
		break;
	}
	case RC_Central:
		break;

	default:
		break;
	}

	//モードごとの初期化処理
	if (pre_mode != mode)
	{
		// BLEラジコンから抜けるときは強制リセット。　↓がCLOSEされるまで。
		//		Dynamically Start Restart Bluetooth(BLE) · Issue #351 · nkolban / esp32 - snippets https ://github.com/nkolban/esp32-snippets/issues/351
		if (pre_mode == RC || pre_mode == RC_Central)
		{
			ESP.restart();
		}

		rpm_trg_L = 0;
		rpm_trg_R = 0;
		pixels.clear();
		switch (mode)
		{
		case DEMO:
		{
			pixels.setPixelColor(0, orange);
			pixels.show();
			break;
		}
		case FOLLOW:
			break;

		case RC:
		{
			pixels.setPixelColor(0, blue);
			pixels.show();
			ble_peripheral_setup();
			break;
		}
		case RC_Central:
		{
			pixels.setPixelColor(3, blue);
			pixels.show();
			ble_central_setup();
			break;
		}
		default:
			break;
		}
	}

	pre_mode = mode;
	delay(20);
}

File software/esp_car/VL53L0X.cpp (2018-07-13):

// Most of the functionality of this library is based on the VL53L0X API
// provided by ST (STSW-IMG005), and some of the explanatory comments are quoted
// or paraphrased from the API source code, API user manual (UM2039), and the
// VL53L0X datasheet.

#include "VL53L0X.h"

// Defines /////////////////////////////////////////////////////////////////////

// The Arduino two-wire interface uses a 7-bit number for the address,
// and sets the last bit correctly based on reads and writes
#define ADDRESS_DEFAULT 0b0101001

// Record the current time to check an upcoming timeout against
#define startTimeout() (timeout_start_ms = millis())

// Check if timeout is enabled (set to nonzero value) and has expired
#define checkTimeoutExpired() (io_timeout > 0 && ((uint16_t)millis() - timeout_start_ms) > io_timeout)

// Decode VCSEL (vertical cavity surface emitting laser) pulse period in PCLKs
// from register value
// based on VL53L0X_decode_vcsel_period()
#define decodeVcselPeriod(reg_val)      (((reg_val) + 1) << 1)

// Encode VCSEL pulse period register value from period in PCLKs
// based on VL53L0X_encode_vcsel_period()
#define encodeVcselPeriod(period_pclks) (((period_pclks) >> 1) - 1)

// Calculate macro period in *nanoseconds* from VCSEL period in PCLKs
// based on VL53L0X_calc_macro_period_ps()
// PLL_period_ps = 1655; macro_period_vclks = 2304
#define calcMacroPeriod(vcsel_period_pclks) ((((uint32_t)2304 * (vcsel_period_pclks) * 1655) + 500) / 1000)

// Constructors ////////////////////////////////////////////////////////////////

VL53L0X::VL53L0X(void)
  : address(ADDRESS_DEFAULT)
  , io_timeout(0) // no timeout
  , did_timeout(false)
{
}

// Public Methods //////////////////////////////////////////////////////////////

void VL53L0X::setWire(TwoWire* wire) {
  myWire = wire;
}
void VL53L0X::setAddress(uint8_t new_addr)
{
  writeReg(I2C_SLAVE_DEVICE_ADDRESS, new_addr & 0x7F);
  address = new_addr;
}

// Initialize sensor using sequence based on VL53L0X_DataInit(),
// VL53L0X_StaticInit(), and VL53L0X_PerformRefCalibration().
// This function does not perform reference SPAD calibration
// (VL53L0X_PerformRefSpadManagement()), since the API user manual says that it
// is performed by ST on the bare modules; it seems like that should work well
// enough unless a cover glass is added.
// If io_2v8 (optional) is true or not given, the sensor is configured for 2V8
// mode.
bool VL53L0X::init(bool io_2v8)
{
  // VL53L0X_DataInit() begin

  // sensor uses 1V8 mode for I/O by default; switch to 2V8 mode if necessary
  if (io_2v8)
  {
    writeReg(VHV_CONFIG_PAD_SCL_SDA__EXTSUP_HV,
      readReg(VHV_CONFIG_PAD_SCL_SDA__EXTSUP_HV) | 0x01); // set bit 0
  }

  // "Set I2C standard mode"
  writeReg(0x88, 0x00);

  writeReg(0x80, 0x01);
  writeReg(0xFF, 0x01);
  writeReg(0x00, 0x00);
  stop_variable = readReg(0x91);
  writeReg(0x00, 0x01);
  writeReg(0xFF, 0x00);
  writeReg(0x80, 0x00);

  // disable SIGNAL_RATE_MSRC (bit 1) and SIGNAL_RATE_PRE_RANGE (bit 4) limit checks
  writeReg(MSRC_CONFIG_CONTROL, readReg(MSRC_CONFIG_CONTROL) | 0x12);

  // set final range signal rate limit to 0.25 MCPS (million counts per second)
  setSignalRateLimit(0.25);

  writeReg(SYSTEM_SEQUENCE_CONFIG, 0xFF);

  // VL53L0X_DataInit() end

  // VL53L0X_StaticInit() begin

  uint8_t spad_count;
  bool spad_type_is_aperture;
  if (!getSpadInfo(&spad_count, &spad_type_is_aperture)) { return false; }

  // The SPAD map (RefGoodSpadMap) is read by VL53L0X_get_info_from_device() in
  // the API, but the same data seems to be more easily readable from
  // GLOBAL_CONFIG_SPAD_ENABLES_REF_0 through _6, so read it from there
  uint8_t ref_spad_map[6];
  readMulti(GLOBAL_CONFIG_SPAD_ENABLES_REF_0, ref_spad_map, 6);

  // -- VL53L0X_set_reference_spads() begin (assume NVM values are valid)

  writeReg(0xFF, 0x01);
  writeReg(DYNAMIC_SPAD_REF_EN_START_OFFSET, 0x00);
  writeReg(DYNAMIC_SPAD_NUM_REQUESTED_REF_SPAD, 0x2C);
  writeReg(0xFF, 0x00);
  writeReg(GLOBAL_CONFIG_REF_EN_START_SELECT, 0xB4);

  uint8_t first_spad_to_enable = spad_type_is_aperture ? 12 : 0; // 12 is the first aperture spad
  uint8_t spads_enabled = 0;

  for (uint8_t i = 0; i < 48; i++)
  {
    if (i < first_spad_to_enable || spads_enabled == spad_count)
    {
      // This bit is lower than the first one that should be enabled, or
      // (reference_spad_count) bits have already been enabled, so zero this bit
      ref_spad_map[i / 8] &= ~(1 << (i % 8));
    }
    else if ((ref_spad_map[i / 8] >> (i % 8)) & 0x1)
    {
      spads_enabled++;
    }
  }

  writeMulti(GLOBAL_CONFIG_SPAD_ENABLES_REF_0, ref_spad_map, 6);

  // -- VL53L0X_set_reference_spads() end

  // -- VL53L0X_load_tuning_settings() begin
  // DefaultTuningSettings from vl53l0x_tuning.h

  writeReg(0xFF, 0x01);
  writeReg(0x00, 0x00);

  writeReg(0xFF, 0x00);
  writeReg(0x09, 0x00);
  writeReg(0x10, 0x00);
  writeReg(0x11, 0x00);

  writeReg(0x24, 0x01);
  writeReg(0x25, 0xFF);
  writeReg(0x75, 0x00);

  writeReg(0xFF, 0x01);
  writeReg(0x4E, 0x2C);
  writeReg(0x48, 0x00);
  writeReg(0x30, 0x20);

  writeReg(0xFF, 0x00);
  writeReg(0x30, 0x09);
  writeReg(0x54, 0x00);
  writeReg(0x31, 0x04);
  writeReg(0x32, 0x03);
  writeReg(0x40, 0x83);
  writeReg(0x46, 0x25);
  writeReg(0x60, 0x00);
  writeReg(0x27, 0x00);
  writeReg(0x50, 0x06);
  writeReg(0x51, 0x00);
  writeReg(0x52, 0x96);
  writeReg(0x56, 0x08);
  writeReg(0x57, 0x30);
  writeReg(0x61, 0x00);
  writeReg(0x62, 0x00);
  writeReg(0x64, 0x00);
  writeReg(0x65, 0x00);
  writeReg(0x66, 0xA0);

  writeReg(0xFF, 0x01);
  writeReg(0x22, 0x32);
  writeReg(0x47, 0x14);
  writeReg(0x49, 0xFF);
  writeReg(0x4A, 0x00);

  writeReg(0xFF, 0x00);
  writeReg(0x7A, 0x0A);
  writeReg(0x7B, 0x00);
  writeReg(0x78, 0x21);

  writeReg(0xFF, 0x01);
  writeReg(0x23, 0x34);
  writeReg(0x42, 0x00);
  writeReg(0x44, 0xFF);
  writeReg(0x45, 0x26);
  writeReg(0x46, 0x05);
  writeReg(0x40, 0x40);
  writeReg(0x0E, 0x06);
  writeReg(0x20, 0x1A);
  writeReg(0x43, 0x40);

  writeReg(0xFF, 0x00);
  writeReg(0x34, 0x03);
  writeReg(0x35, 0x44);

  writeReg(0xFF, 0x01);
  writeReg(0x31, 0x04);
  writeReg(0x4B, 0x09);
  writeReg(0x4C, 0x05);
  writeReg(0x4D, 0x04);

  writeReg(0xFF, 0x00);
  writeReg(0x44, 0x00);
  writeReg(0x45, 0x20);
  writeReg(0x47, 0x08);
  writeReg(0x48, 0x28);
  writeReg(0x67, 0x00);
  writeReg(0x70, 0x04);
  writeReg(0x71, 0x01);
  writeReg(0x72, 0xFE);
  writeReg(0x76, 0x00);
  writeReg(0x77, 0x00);

  writeReg(0xFF, 0x01);
  writeReg(0x0D, 0x01);

  writeReg(0xFF, 0x00);
  writeReg(0x80, 0x01);
  writeReg(0x01, 0xF8);

  writeReg(0xFF, 0x01);
  writeReg(0x8E, 0x01);
  writeReg(0x00, 0x01);
  writeReg(0xFF, 0x00);
  writeReg(0x80, 0x00);

  // -- VL53L0X_load_tuning_settings() end

  // "Set interrupt config to new sample ready"
  // -- VL53L0X_SetGpioConfig() begin
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

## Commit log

2018-06-05 project add
    [esp_car.brd, esp_car.sch]
2018-06-06 daliy commit
    [esp_car.brd, esp_car.sch]
2018-06-10 chematic v1.0
    [esp_car.brd, esp_car.sch]
2018-06-10 board test
    [esp_car.brd, esp_car.sch]
2018-06-13 sche fix,board test
    [esp_car.brd, esp_car.sch]
2018-06-13 pdf add
    [esp_car.brd, esp_car.sch]
2018-06-15 from office
    [esp_car.brd, esp_car.sch]
2018-06-18 art work
    [esp_car.brd, esp_car.sch]
2018-06-19 ユニバーサル部分追加、NETCLASS調整
    [esp_car.brd, esp_car.sch]
2018-06-19 配線良し
    [esp_car.brd]
2018-06-19 wire 100% 初版
    [esp_car.brd, esp_car.sch]
2018-06-20 5vレギュレータをLDOに変更、配線100% v2
    [esp_car.brd, esp_car.sch]
2018-06-20 電源用MOSFET追加、VDD見直し
    [esp_car.brd, esp_car.sch]
2018-06-20 airwireなし
    [esp_car.brd]
2018-06-21 esp32のviaの径設定ミス修正、NMOS向き修正、配線やり直し完了
    [esp_car.brd, esp_car.sch]
2018-06-21 PDF,ガーバー出力
    [esp_car.GBL, esp_car.GBO, esp_car.GBP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]
2018-06-21 GNDを太く。サーマルランドが細かった
    [esp_car.brd]
2018-06-21 コンデンサの向きを修正
    [esp_car.GBL, esp_car.GBO, esp_car.GBP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]
2018-06-22 c1,c9,r2,r3,r4 微修正 nmos向き修正、so8シルク追加
    [esp_car.GBL, esp_car.GBO, esp_car.GBP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]
2018-06-22 基板FIX、発注
    [esp_car.GBL, esp_car.GBO, esp_car.GBP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]
2018-06-23 add board pdf
2018-07-08 code add
    [esp_car.brd]
2018-07-13 add mecha
    [Body.stl, head.stl]
2018-07-13 tof sensor
2018-07-16 抵抗値の修正
    [esp_car.brd, esp_car.sch]
2018-07-16 BLEテスト
2018-07-16 探索実装
2018-07-17 sarch object
    [esp_car.brd]
2018-07-17 とりあえず。
2018-07-17 led space
    [Body.stl]
2018-07-17 接合部の付け根を太く
    [head.stl]
2018-07-22 qeiテスト
2018-07-22 速度制御
2018-07-22 BLEをいろいろおためし
2018-07-22 パーツ変更
2018-07-22 コメント修正
2018-07-24 バッテリーポート変更、BLEのモジュールを適当に配置
    [esp_car.sch]
2018-07-25 BLEラジコン実装
2018-07-26 RCの感度変更
2018-07-28 instractuions in case(switch) needs {} ... why?
2018-07-28 ubit ble uart mode (not yet text parser)
2018-07-30 ubit 連携OK
2018-08-02 制御ゲインを微調整。無駄ソース削除、リードミー修正

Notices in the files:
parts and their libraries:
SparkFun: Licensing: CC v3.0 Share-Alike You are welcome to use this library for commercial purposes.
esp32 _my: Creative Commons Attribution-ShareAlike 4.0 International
